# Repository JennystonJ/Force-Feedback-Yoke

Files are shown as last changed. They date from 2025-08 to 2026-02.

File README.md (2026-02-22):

# Force Feedback Yoke
A DIY force feedback flight simulator yoke using brushless motors, load cells, and custom firmware to provide simulated control forces.

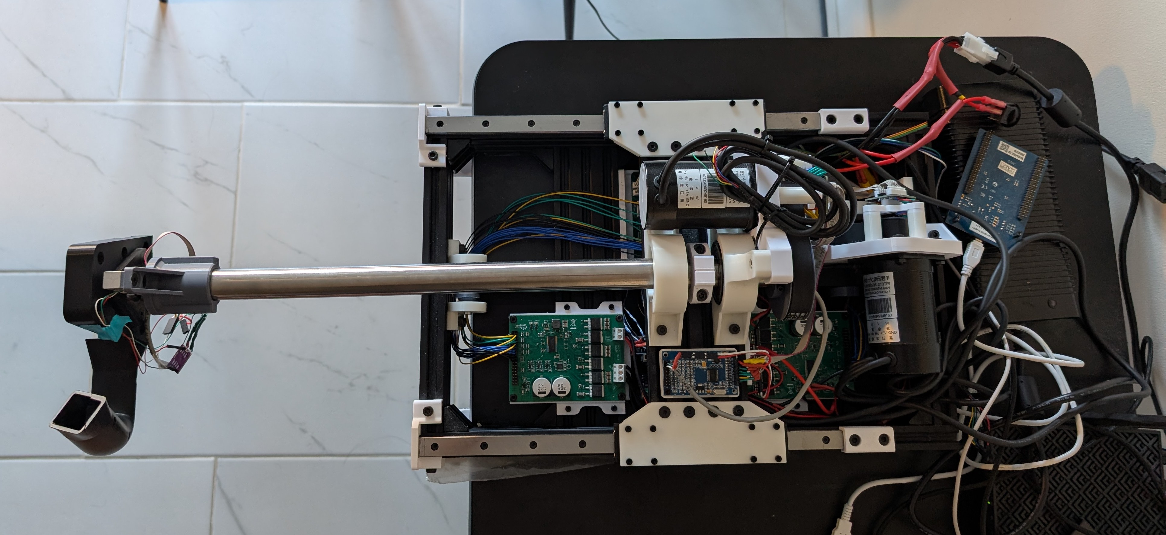
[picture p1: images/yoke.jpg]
Yoke Picture


---

## Overview
- BLDC motors for pitch and roll using torque control.
- Support for load cells. Currently used for force feedback assist (reduces drag felt by user).
- STM32 microcontroller running custom firmware with FOC inspired by SimpleFOC.
- Desktop app for monitoring, setting parameters, handling communication between device and Microsoft Flight Simulator, and calculating forces.

## Features
- Support for 2 axis current/torque control.
- Force feedback assist using load cells to reduce drag.
- USB HID communication.
- Support for constant, spring, and damper effects on both axes.
- Axes travel is software adjustable using the motor as a virtual stopper.

## Technical Details
- Motors: 2 * 57BL95S06-210TF9
- Motor Drivers: 2 * DRV8301 boards
- Microcontroller: STM32H743VGT6
- Sensors:
	- 2 * three phase shunt-based in-line current sensors (INA241)
	- 2 * encoders using AB output (65536 CPR) for lower latency (MT6835)
	- 2 * load cells (20kg) (roll load cell support for mechanical is in progress)
- Software: C firmware, C# desktop app

## Mechanical
- Total pitch travel: ~177 mm, roll travel: ~270 deg
- 3D printed components, aluminum V-slot extrusion for frame. T-slot is also compatible.
- Bearings on all axes, two linear guide rails for linear motion on pitch axis.
- Two-stage belt drive for pitch axis, single belt for roll axis.
- Designed to be modular.

## Desktop App
- Displays live axes positions, and axes force/torque
- Implements custom USB HID communication with device and communication with Microsoft Flight Simulator through SimConnect API.
- Currently supports 2 different force feedback effects, with more being added and existing effects being refined:
	- Supported effects
		- Airspeed stiffness (increases centering force with airspeed)
		- Elevator weight (a constant elevator down force with engine RPM dependent self-centering force).
- Adjustable gains for all force feedback effects in GUI for both pitch and roll axes.
- Travel for both axes are adjustable in GUI.

## Acknowledgements
Algorithms (Clarke & Park transforms) from [SimpleFOC](https://github.com/simplefoc/Arduino-FOC) (MIT License). See LICENSES/LICENSE-SIMPLEFOC.txt for full license.

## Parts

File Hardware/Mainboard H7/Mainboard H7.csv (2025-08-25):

Reference | Qty | Value | DNP | Exclude from BOM | Exclude from Board | Footprint | Datasheet
C1,C2,C3,C4,C5,C6,C7,C8 | 8 | 0.1uF |  |  |  | Capacitor_SMD:C_0603_1608Metric_Pad1.08x0.95mm_HandSolder | ~
J1 | 1 | Encoder_2 |  |  |  | Connector_JST:JST_PH_B9B-PH-K_1x09_P2.00mm_Vertical | ~
J2 | 1 | Encoder_1_AB |  |  |  | Connector_JST:JST_PH_B4B-PH-K_1x04_P2.00mm_Vertical | ~
J3 | 1 | M1_Communication |  |  |  | Connector_PinHeader_2.54mm:PinHeader_2x04_P2.54mm_Vertical | ~
J4 | 1 | M1_Driver |  |  |  | Connector_PinHeader_2.54mm:PinHeader_2x06_P2.54mm_Vertical | ~
J5 | 1 | M2_Communication |  |  |  | Connector_PinHeader_2.54mm:PinHeader_2x04_P2.54mm_Vertical | ~
J6 | 1 | M2_Driver |  |  |  | Connector_PinHeader_2.54mm:PinHeader_2x06_P2.54mm_Vertical | ~
J7 | 1 | I2C Expansion 1 |  |  |  | Connector_JST:JST_PH_B6B-PH-K_1x06_P2.00mm_Vertical | ~
J8 | 1 | I2C Expansion 2 |  |  |  | Connector_JST:JST_PH_B6B-PH-K_1x06_P2.00mm_Vertical | ~
J9 | 1 | Encoder_1 |  |  |  | Connector_JST:JST_PH_B9B-PH-K_1x09_P2.00mm_Vertical | ~
J10 | 1 | Encoder_2_AB |  |  |  | Connector_JST:JST_PH_B4B-PH-K_1x04_P2.00mm_Vertical | ~
J11 | 1 | ADC_2 |  |  |  | Connector_JST:JST_PH_B10B-PH-K_1x10_P2.00mm_Vertical | ~
J12 | 1 | ADC_1 |  |  |  | Connector_JST:JST_PH_B10B-PH-K_1x10_P2.00mm_Vertical | ~
J13 | 1 | Yoke_Handle |  |  |  | Connector_JST:JST_PH_B10B-PH-K_1x10_P2.00mm_Vertical | ~
J14 | 1 | M1_Current_Sense |  |  |  | Connector_JST:JST_PH_B8B-PH-K_1x08_P2.00mm_Vertical | ~
J15 | 1 | M2_Current_Sense |  |  |  | Connector_JST:JST_PH_B8B-PH-K_1x08_P2.00mm_Vertical | ~
J16 | 1 | PROBE |  |  |  | Connector_PinHeader_2.54mm:PinHeader_1x03_P2.54mm_Vertical | ~
J17 | 1 | UART |  |  |  | Connector_PinHeader_2.54mm:PinHeader_1x04_P2.54mm_Vertical | ~
J18 | 1 | Power Output |  |  |  | Connector_PinHeader_2.54mm:PinHeader_1x02_P2.54mm_Vertical | ~
J19 | 1 | CAN |  |  |  | Connector_PinHeader_2.54mm:PinHeader_1x05_P2.54mm_Vertical | ~
R1,R2,R3,R4 | 4 | 10k |  |  |  | Resistor_SMD:R_0603_1608Metric_Pad0.98x0.95mm_HandSolder | ~
R5,R6,R7,R8 | 4 | 4.7k |  |  |  | Resistor_SMD:R_0603_1608Metric_Pad0.98x0.95mm_HandSolder | ~
R9 | 1 | 1k |  |  |  | Resistor_SMD:R_0603_1608Metric_Pad0.98x0.95mm_HandSolder | ~
SW1 | 1 | SW_Push |  |  |  | Connector_JST:JST_PH_B2B-PH-K_1x02_P2.00mm_Vertical | ~
U1 | 1 | ~ |  |  |  | FK743M3:FK743M3-VGT6

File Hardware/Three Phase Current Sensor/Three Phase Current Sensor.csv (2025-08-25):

Reference | Qty | Value | DNP | Exclude from BOM | Exclude from Board | Footprint | Datasheet
C1,C8 | 2 | 10uF |  |  |  | Capacitor_SMD:C_0603_1608Metric | ~
C2 | 1 | 10nF |  |  |  | Capacitor_SMD:C_0603_1608Metric | ~
C3,C4,C5,C6,C7 | 5 | 0.1uF |  |  |  | Capacitor_SMD:C_0603_1608Metric | ~
H1,H2 | 2 | MountingHole |  | Excluded from BOM |  | MountingHole:MountingHole_2.2mm_M2 | ~
J1 | 1 | Current Sense Out |  |  |  | Connector_JST:JST_PH_B8B-PH-K_1x08_P2.00mm_Vertical | ~
J2,J3,J4 | 3 | Conn_01x02 |  |  |  | TB005_762_02BE:CUI_TB005-762-02BE | ~
J5 | 1 | Power |  |  |  | Connector_Molex:Molex_KK-254_AE-6410-02A_1x02_P2.54mm_Vertical | ~
R1,R2 | 2 | 10k |  |  |  | Resistor_SMD:R_0603_1608Metric | ~
R3,R4,R5 | 3 | 5m |  |  |  | Resistor_SMD:R_2512_6332Metric | ~
U1 | 1 | TLV9151IDBVR |  |  |  | TLV9151:DBV0005A-MFG | TLV9151IDBVR
U2,U3,U4 | 3 | INA240A1D |  |  |  | Package_SO:SOIC-8_3.9x4.9mm_P1.27mm | http://www.ti.com/lit/ds/symlink/ina240.pdf

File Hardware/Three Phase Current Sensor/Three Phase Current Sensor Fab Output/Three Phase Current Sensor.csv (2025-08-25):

Reference | Qty | Value | DNP | Exclude from BOM | Exclude from Board | Footprint | Datasheet
C1,C8 | 2 | 10uF |  |  |  | Capacitor_SMD:C_0603_1608Metric | ~
C2 | 1 | 10nF |  |  |  | Capacitor_SMD:C_0603_1608Metric | ~
C3,C4,C5,C6,C7 | 5 | 0.1uF |  |  |  | Capacitor_SMD:C_0603_1608Metric | ~
H1,H2,H3,H4 | 4 | MountingHole |  | Excluded from BOM |  | MountingHole:MountingHole_2.2mm_M2 | ~
J1 | 1 | Current Sense Out |  |  |  | Connector_JST:JST_PH_B8B-PH-K_1x08_P2.00mm_Vertical | ~
J2,J3,J4 | 3 | Conn_01x02 |  |  |  | TerminalBlock_Phoenix:TerminalBlock_Phoenix_MKDS-1,5-2-5.08_1x02_P5.08mm_Horizontal | ~
J5 | 1 | Power |  |  |  | Connector_Molex:Molex_KK-254_AE-6410-02A_1x02_P2.54mm_Vertical | ~
R1,R2 | 2 | 10k |  |  |  | Resistor_SMD:R_0603_1608Metric | ~
R3,R4,R5 | 3 | 5m |  |  |  | Resistor_SMD:R_2512_6332Metric | ~
R6 | 1 | 50 |  |  |  | Resistor_SMD:R_0603_1608Metric | ~
U1 | 1 | LMV796MFX |  |  |  | TLV9151:DBV0005A-MFG | TLV9151IDBVR
U2,U3,U4 | 3 | INA241A2IDR |  |  |  | Package_SO:SOIC-8_3.9x4.9mm_P1.27mm | http://www.ti.com/lit/ds/symlink/ina240.pdf

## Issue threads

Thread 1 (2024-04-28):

yoke

1766029053, 2024-04-28:
This project looks cool, are you still working on it

JennystonJ, 2024-05-01:
The force feedback yoke is still in development. While there was a hiatus, I've been focusing on designing its mechanical parts, mostly using 3D printed parts and aluminum extrusion. I plan on returning to the code soon. Thank you for your interest. Feel free to ask if you have any more questions!

1766029053, 2024-05-13:
Do you have any relevant communication platform, so as to facilitate our communication

JennystonJ, 2024-07-01:
I've created a Discord server for the project. Here is the link: https://discord.gg/AJm64B3pnq

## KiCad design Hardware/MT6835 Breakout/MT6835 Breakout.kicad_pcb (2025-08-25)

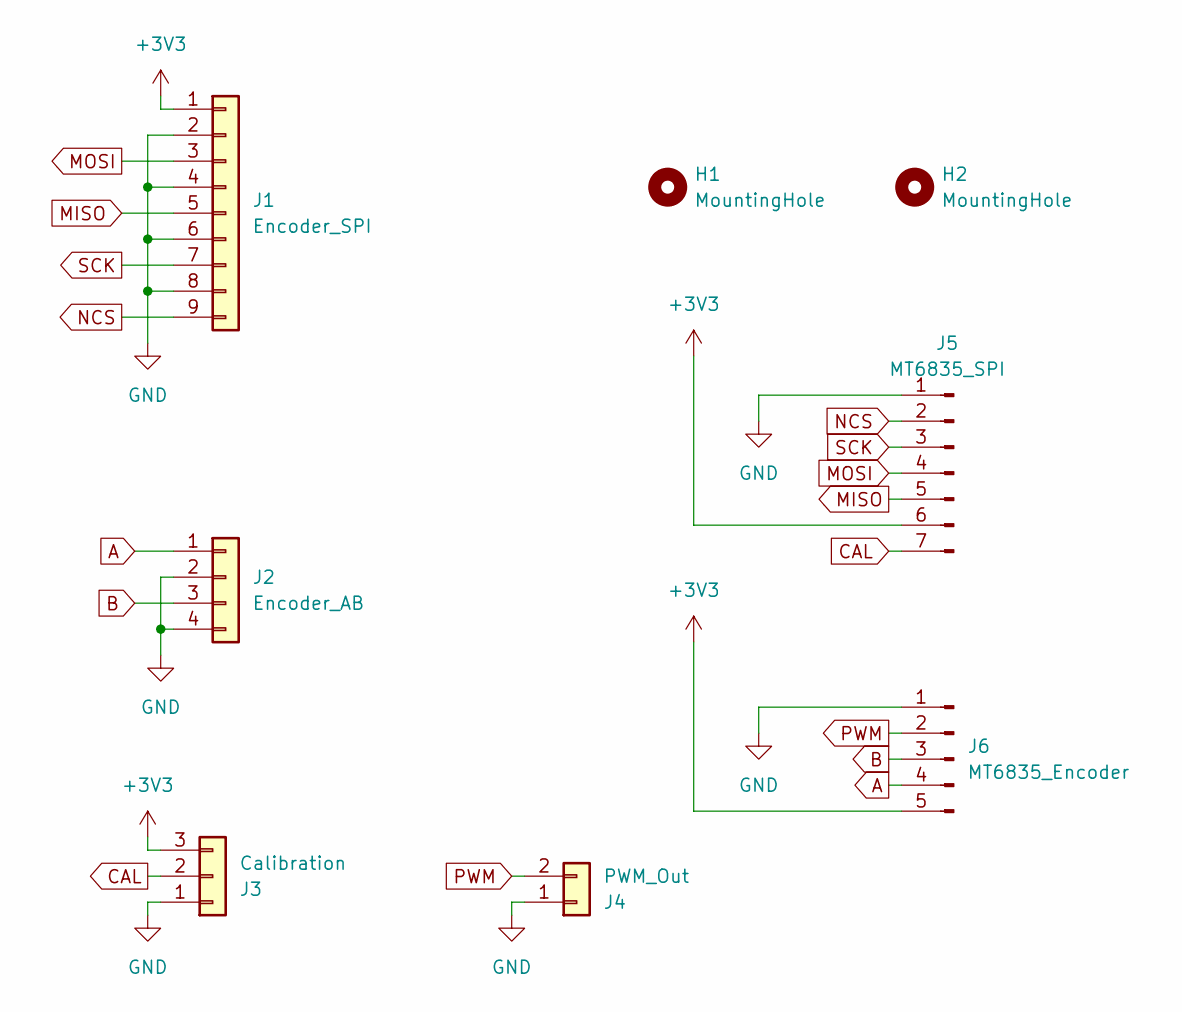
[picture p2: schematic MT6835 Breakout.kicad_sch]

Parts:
H1, H2: MountingHole; MountingHole_2.2mm_M2
J1: Encoder_SPI; JST_PH_B9B-PH-K_1x09_P2.00mm_Vertical
J2: Encoder_AB; JST_PH_B4B-PH-K_1x04_P2.00mm_Vertical
J3: Calibration; PinHeader_1x03_P2.54mm_Vertical
J4: PWM_Out; PinHeader_1x02_P2.54mm_Vertical
J5: MT6835_SPI; PinHeader_1x07_P2.54mm_Vertical
J6: MT6835_Encoder; PinHeader_1x05_P2.54mm_Vertical

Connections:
+3V3: J1.1, J3.3, J5.6, J6.5
A: J2.1, J6.4
B: J2.3, J6.3
CAL: J3.2, J5.7
GND: J1.2, J1.4, J1.6, J1.8, J2.2, J2.4, J3.1, J4.1, J5.1, J6.1
MISO: J1.5, J5.5
MOSI: J1.3, J5.4
NCS: J1.9, J5.2
PWM: J4.2, J6.2
SCK: J1.7, J5.3

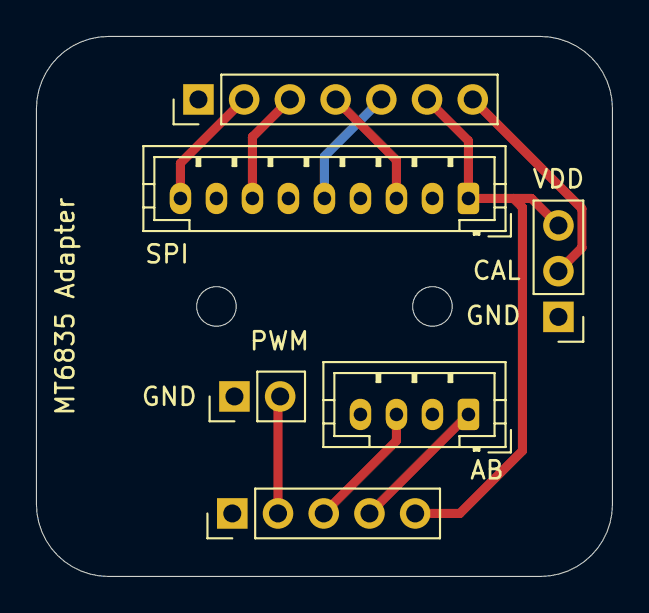
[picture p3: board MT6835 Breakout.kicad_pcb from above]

Board: 2 copper layers, 32.0 x 30.0 mm, 8 parts (0 on the bottom side), 10 nets.

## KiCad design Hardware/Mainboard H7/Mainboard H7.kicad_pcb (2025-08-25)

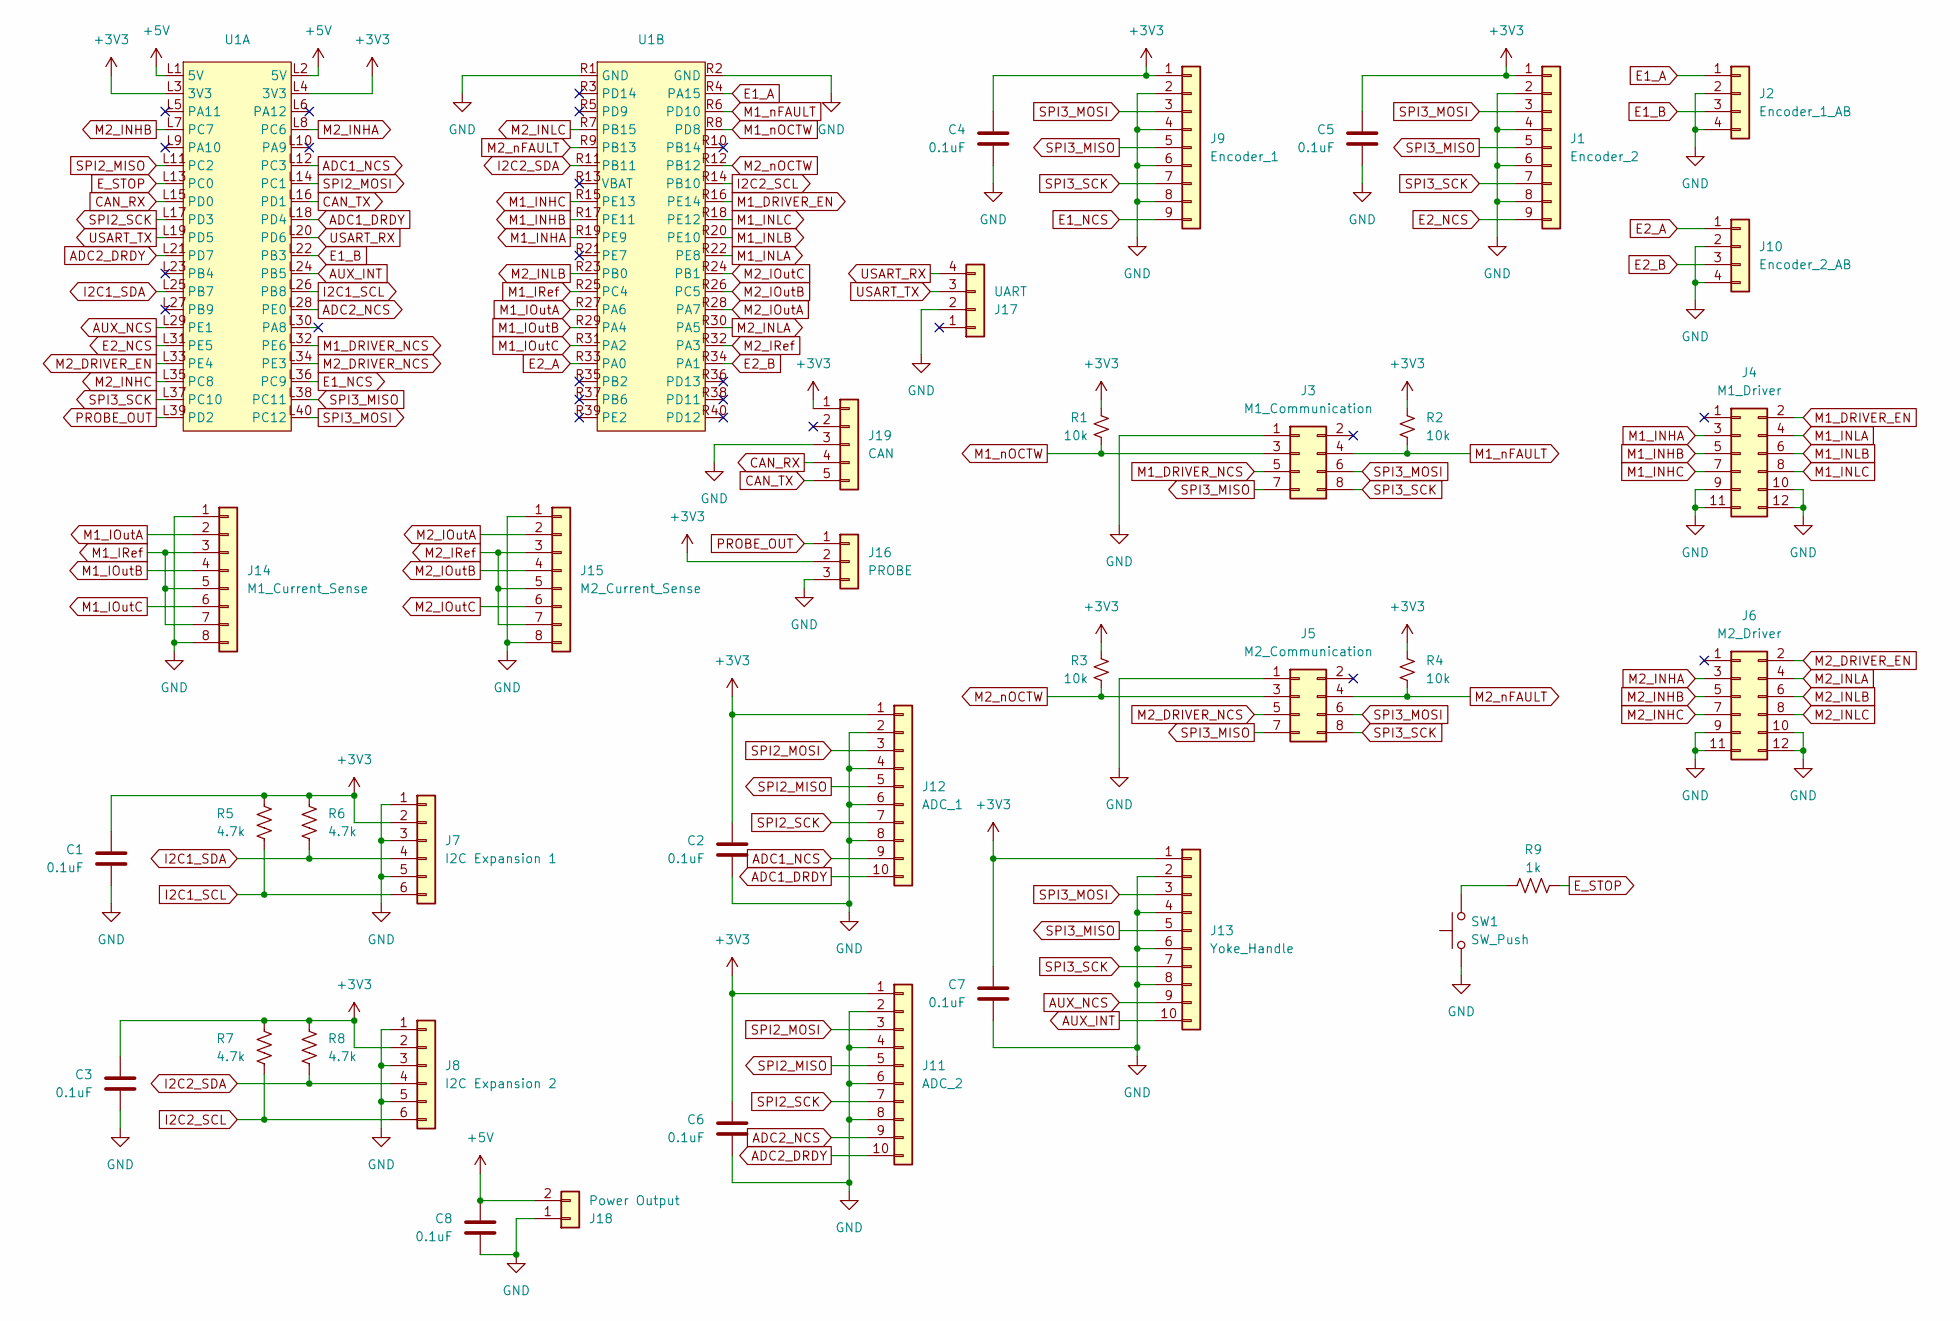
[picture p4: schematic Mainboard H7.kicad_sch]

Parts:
C1, C2, C3, C4, C5, C6, C7, C8: 0.1uF; C_0603_1608Metric_Pad1.08x0.95mm_HandSolder
J1: Encoder_2; JST_PH_B9B-PH-K_1x09_P2.00mm_Vertical
J2: Encoder_1_AB; JST_PH_B4B-PH-K_1x04_P2.00mm_Vertical
J3: M1_Communication; PinHeader_2x04_P2.54mm_Vertical
J4: M1_Driver; PinHeader_2x06_P2.54mm_Vertical
J5: M2_Communication; PinHeader_2x04_P2.54mm_Vertical
J6: M2_Driver; PinHeader_2x06_P2.54mm_Vertical
J7: I2C Expansion 1; JST_PH_B6B-PH-K_1x06_P2.00mm_Vertical
J8: I2C Expansion 2; JST_PH_B6B-PH-K_1x06_P2.00mm_Vertical
J9: Encoder_1; JST_PH_B9B-PH-K_1x09_P2.00mm_Vertical
J10: Encoder_2_AB; JST_PH_B4B-PH-K_1x04_P2.00mm_Vertical
J11: ADC_2; JST_PH_B10B-PH-K_1x10_P2.00mm_Vertical
J12: ADC_1; JST_PH_B10B-PH-K_1x10_P2.00mm_Vertical
J13: Yoke_Handle; JST_PH_B10B-PH-K_1x10_P2.00mm_Vertical
J14: M1_Current_Sense; JST_PH_B8B-PH-K_1x08_P2.00mm_Vertical
J15: M2_Current_Sense; JST_PH_B8B-PH-K_1x08_P2.00mm_Vertical
J16: PROBE; PinHeader_1x03_P2.54mm_Vertical
J17: UART; PinHeader_1x04_P2.54mm_Vertical
J18: Power Output; PinHeader_1x02_P2.54mm_Vertical
J19: CAN; PinHeader_1x05_P2.54mm_Vertical
R1, R2, R3, R4: 10k; R_0603_1608Metric_Pad0.98x0.95mm_HandSolder
R5, R6, R7, R8: 4.7k; R_0603_1608Metric_Pad0.98x0.95mm_HandSolder
R9: 1k; R_0603_1608Metric_Pad0.98x0.95mm_HandSolder
SW1: SW_Push; JST_PH_B2B-PH-K_1x02_P2.00mm_Vertical
U1: FK743M3-VGT6

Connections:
+3V3: C1.1, C2.1, C3.1, C4.1, C5.1, C6.1, C7.1, J1.1, J7.2, J8.2, J9.1, J11.1, J12.1, J13.1, J16.2, J19.1, R1.1, R2.1, R3.1, R4.1, R5.1, R6.1, R7.1, R8.1, U1.L3 (3V3), U1.L4 (3V3)
+5V: C8.1, J18.2, U1.L1 (5V), U1.L2 (5V)
ADC1_DRDY: J12.10, U1.L18 (PD4)
ADC1_NCS: J12.9, U1.L12 (PC3)
ADC2_DRDY: J11.10, U1.L21 (PD7)
ADC2_NCS: J11.9, U1.L28 (PE0)
AUX_INT: J13.10, U1.L24 (PB5)
AUX_NCS: J13.9, U1.L29 (PE1)
CAN_RX: J19.4, U1.L15 (PD0)
CAN_TX: J19.5, U1.L16 (PD1)
E1_A: J2.1, U1.R4 (PA15)
E1_B: J2.3, U1.L22 (PB3)
E1_NCS: J9.9, U1.L36 (PC9)
E2_A: J10.1, U1.R33 (PA0)
E2_B: J10.3, U1.R34 (PA1)
E2_NCS: J1.9, U1.L31 (PE5)
E_STOP: R9.1, U1.L13 (PC0)
GND: C1.2, C2.2, C3.2, C4.2, C5.2, C6.2, C7.2, C8.2, J1.2, J1.4, J1.6, J1.8, J2.2, J2.4, J3.1, J4.9, J4.10, J4.11, J4.12, J5.1, J6.9, J6.10, J6.11, J6.12, J7.1, J7.3, J7.5, J8.1, J8.3, J8.5, J9.2, J9.4, J9.6, J9.8, J10.2, J10.4, J11.2, J11.4, J11.6, J11.8, J12.2, J12.4, J12.6, J12.8, J13.2, J13.4, J13.6, J13.8, J14.1, J14.8, J15.1, J15.8, J16.3, J17.2, J18.1, J19.3, SW1.1, U1.R1 (GND), U1.R2 (GND)
I2C1_SCL: J7.6, R5.2, U1.L26 (PB8)
I2C1_SDA: J7.4, R6.2, U1.L25 (PB7)
I2C2_SCL: J8.6, R7.2, U1.R14 (PB10)
I2C2_SDA: J8.4, R8.2, U1.R11 (PB11)
M1_DRIVER_EN: J4.2, U1.R16 (PE14)
M1_DRIVER_NCS: J3.5, U1.L32 (PE6)
M1_INHA: J4.3, U1.R19 (PE9)
M1_INHB: J4.5, U1.R17 (PE11)
M1_INHC: J4.7, U1.R15 (PE13)
M1_INLA: J4.4, U1.R22 (PE8)
M1_INLB: J4.6, U1.R20 (PE10)
M1_INLC: J4.8, U1.R18 (PE12)
M1_IOutA: J14.2, U1.R27 (PA6)
M1_IOutB: J14.4, U1.R29 (PA4)
M1_IOutC: J14.6, U1.R31 (PA2)
M1_IRef: J14.3, J14.5, J14.7, U1.R25 (PC4)
M1_nFAULT: J3.4, R2.2, U1.R6 (PD10)
M1_nOCTW: J3.3, R1.2, U1.R8 (PD8)
M2_DRIVER_EN: J6.2, U1.L33 (PE4)
M2_DRIVER_NCS: J5.5, U1.L34 (PE3)
M2_INHA: J6.3, U1.L8 (PC6)
M2_INHB: J6.5, U1.L7 (PC7)
M2_INHC: J6.7, U1.L35 (PC8)
M2_INLA: J6.4, U1.R30 (PA5)
M2_INLB: J6.6, U1.R23 (PB0)
M2_INLC: J6.8, U1.R7 (PB15)
M2_IOutA: J15.2, U1.R28 (PA7)
M2_IOutB: J15.4, U1.R26 (PC5)
M2_IOutC: J15.6, U1.R24 (PB1)
M2_IRef: J15.3, J15.5, J15.7, U1.R32 (PA3)
M2_nFAULT: J5.4, R4.2, U1.R9 (PB13)
M2_nOCTW: J5.3, R3.2, U1.R12 (PB12)
unnamed: R9.2, SW1.2
PROBE_OUT: J16.1, U1.L39 (PD2)
SPI2_MISO: J11.5, J12.5, U1.L11 (PC2)
SPI2_MOSI: J11.3, J12.3, U1.L14 (PC1)
SPI2_SCK: J11.7, J12.7, U1.L17 (PD3)
SPI3_MISO: J1.5, J3.7, J5.7, J9.5, J13.5, U1.L38 (PC11)
SPI3_MOSI: J1.3, J3.6, J5.6, J9.3, J13.3, U1.L40 (PC12)
SPI3_SCK: J1.7, J3.8, J5.8, J9.7, J13.7, U1.L37 (PC10)
USART_RX: J17.4, U1.L20 (PD6)
USART_TX: J17.3, U1.L19 (PD5)

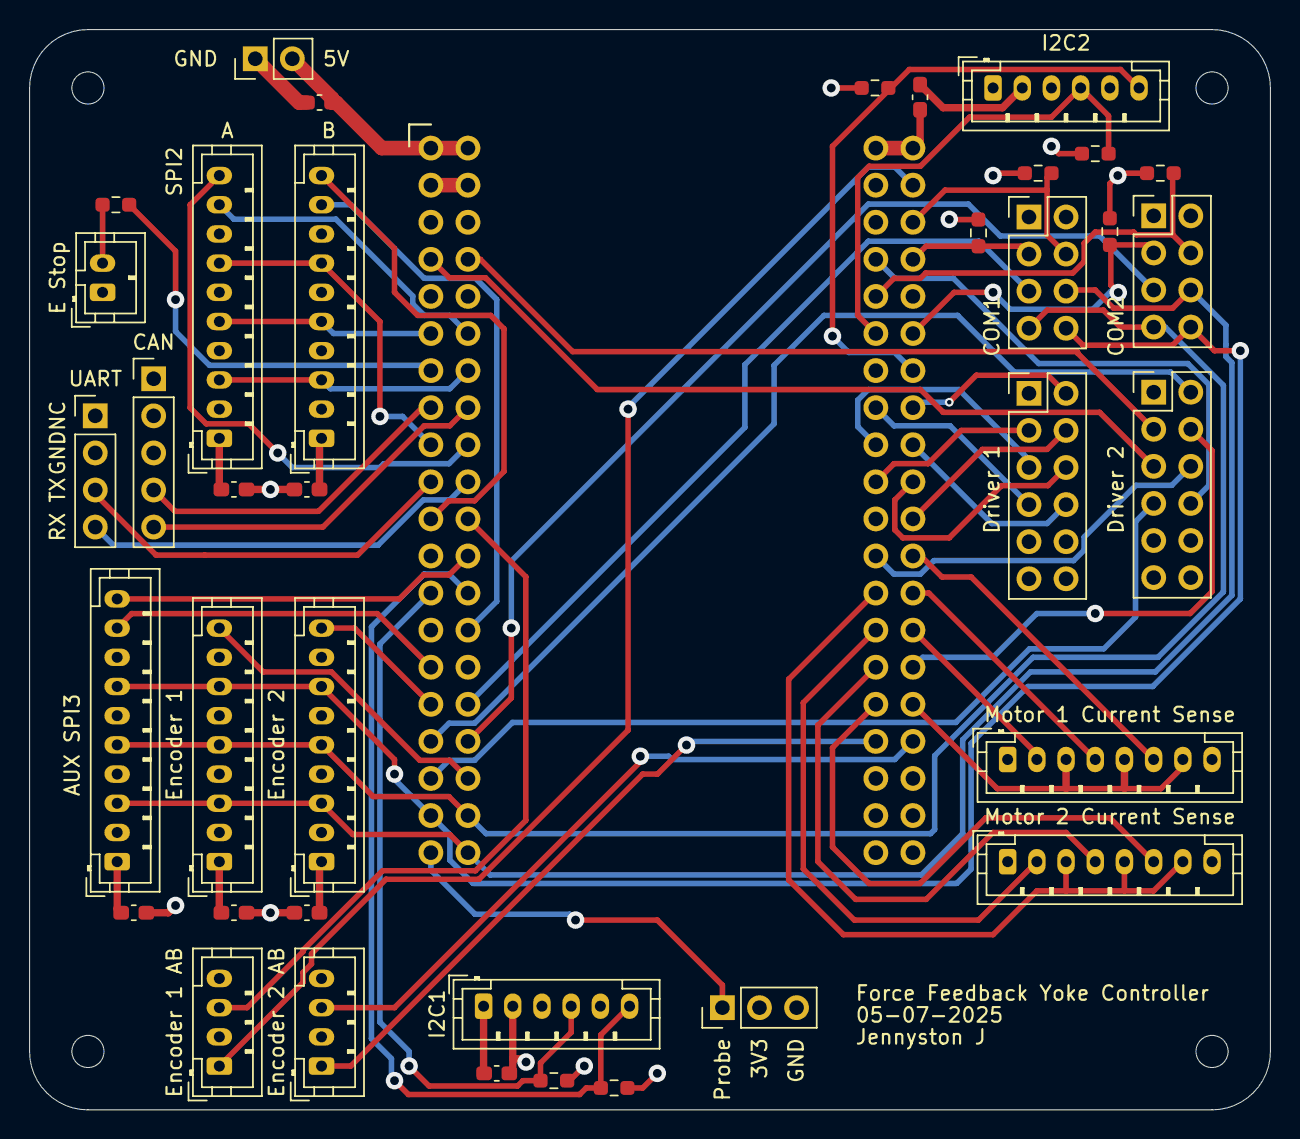
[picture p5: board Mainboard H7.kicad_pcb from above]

Board: 4 copper layers, 85.0 x 74.0 mm, 38 parts (0 on the bottom side), 60 nets.

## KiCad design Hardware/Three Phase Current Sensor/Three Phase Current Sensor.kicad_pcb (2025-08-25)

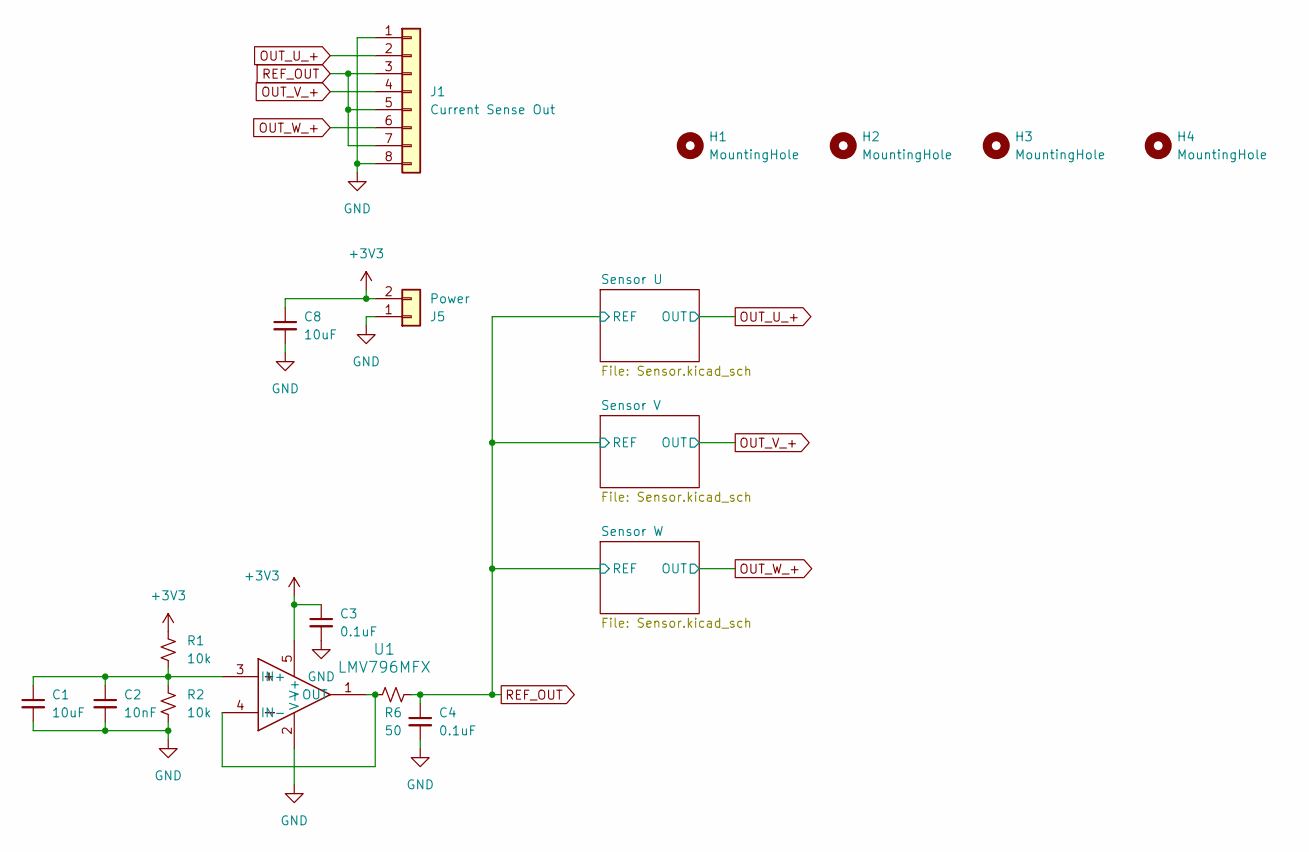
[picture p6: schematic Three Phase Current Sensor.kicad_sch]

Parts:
C1, C8: 10uF; C_0603_1608Metric
C2: 10nF; C_0603_1608Metric
C3, C4: 0.1uF; C_0603_1608Metric
H1, H2, H3, H4: MountingHole; MountingHole_2.2mm_M2
J1: Current Sense Out; JST_PH_B8B-PH-K_1x08_P2.00mm_Vertical
J5: Power; Molex_KK-254_AE-6410-02A_1x02_P2.54mm_Vertical
R1, R2: 10k; R_0603_1608Metric
R6: 50; R_0603_1608Metric
U1: LMV796MFX; DBV0005A-MFG

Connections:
+3V3: C3.1, C8.1, J5.2, R1.2, U1.5 (V+); also elsewhere on the board
GND: C1.2, C2.2, C3.2, C4.2, C8.2, J1.1, J1.8, J5.1, R2.1, U1.2 (V-); also elsewhere on the board
unnamed: C1.1, C2.1, R1.1, R2.2, U1.3 (IN+)
unnamed: R6.2, U1.1 (OUT), U1.4 (IN-)
OUT_U_+: J1.2; also elsewhere on the board
OUT_V_+: J1.4; also elsewhere on the board
OUT_W_+: J1.6; also elsewhere on the board
REF_OUT: C4.1, J1.3, J1.5, J1.7, R6.1; also elsewhere on the board

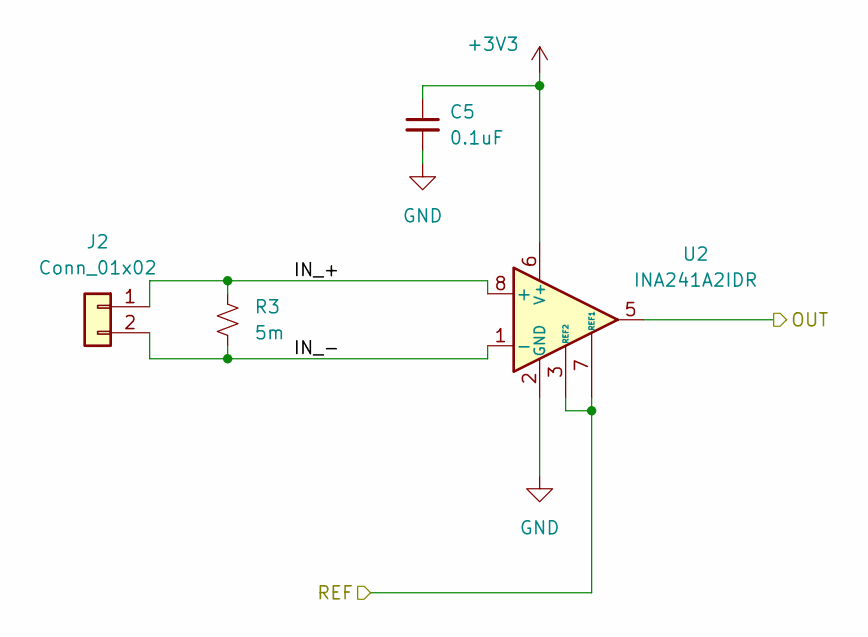
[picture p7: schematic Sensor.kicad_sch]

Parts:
C5: 0.1uF; C_0603_1608Metric
J2: Conn_01x02; TerminalBlock_Phoenix_MKDS-1,5-2-5.08_1x02_P5.08mm_Horizont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
R3: 5m; R_2512_6332Metric
U2: INA241A2IDR; SOIC-8_3.9x4.9mm_P1.27mm

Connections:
+3V3: C5.1, U2.6 (V+); also elsewhere on the board
/Sensor U/IN_+: J2.1, R3.1, U2.8 (+)
/Sensor U/IN_-: J2.2, R3.2, U2.1 (-)
GND: C5.2, U2.2 (GND), U2.4 (GND); also elsewhere on the board
OUT_U_+: U2.5; also elsewhere on the board
REF_OUT: U2.3 (REF2), U2.7 (REF1); also elsewhere on the board

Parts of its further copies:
C6, C7: 0.1uF; C_0603_1608Metric
J3, J4: Conn_01x02; TerminalBlock_Phoenix_MKDS-1,5-2-5.08_1x02_P5.08mm_Horizont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
R4, R5: 5m; R_2512_6332Metric
U3, U4: INA241A2IDR; SOIC-8_3.9x4.9mm_P1.27mm

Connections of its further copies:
+3V3: C6.1, C7.1, U3.6 (V+), U4.6 (V+); also elsewhere on the board
/Sensor V/IN_+: J3.1, R4.1, U3.8 (+)
/Sensor V/IN_-: J3.2, R4.2, U3.1 (-)
/Sensor W/IN_+: J4.1, R5.1, U4.8 (+)
/Sensor W/IN_-: J4.2, R5.2, U4.1 (-)
GND: C6.2, C7.2, U3.2 (GND), U3.4 (GND), U4.2 (GND), U4.4 (GND); also elsewhere on the board
OUT_V_+: U3.5; also elsewhere on the board
OUT_W_+: U4.5; also elsewhere on the board
REF_OUT: U3.3 (REF2), U3.7 (REF1), U4.3 (REF2), U4.7 (REF1); also elsewhere on the board

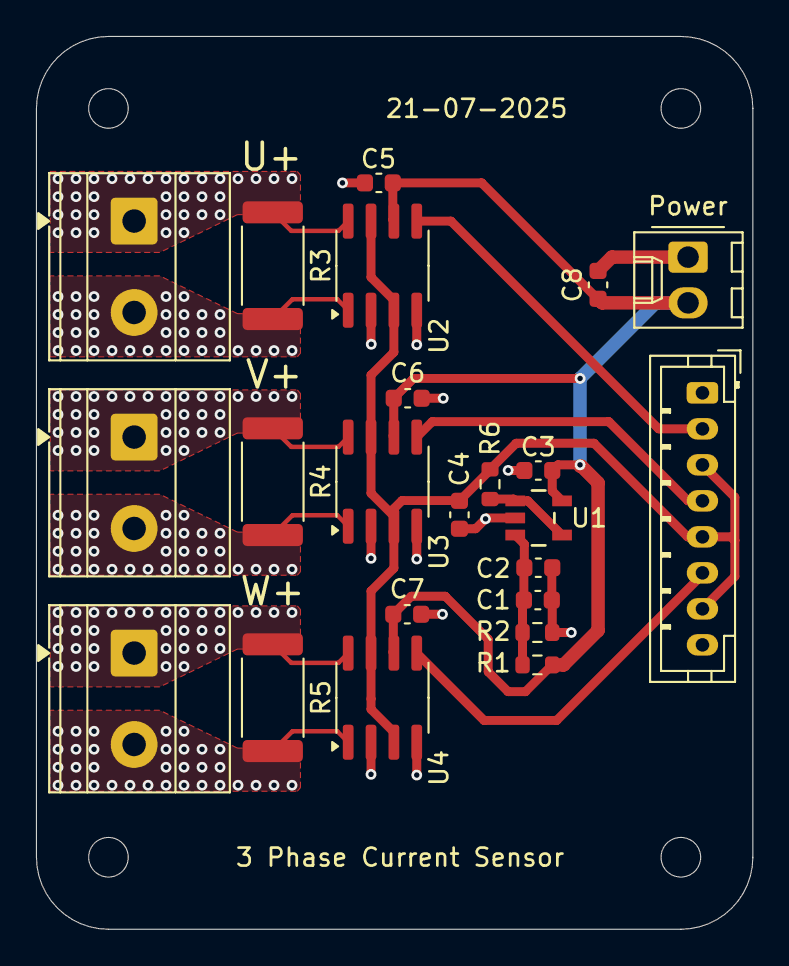
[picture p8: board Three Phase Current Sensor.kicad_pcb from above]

Board: 2 copper layers, 39.8 x 49.6 mm, 27 parts (0 on the bottom side), 14 nets.

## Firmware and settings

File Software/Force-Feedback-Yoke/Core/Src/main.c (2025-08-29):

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
/* Includes ------------------------------------------------------------------*/
#include "main.h"
#include "usb_device.h"

/* USER CODE BEGIN Includes */
#include "bsp.h"
#include "bsp_it.h"
#include "app.h"
/* USER CODE END Includes */

ADC_HandleTypeDef hadc1;
ADC_HandleTypeDef hadc2;

FDCAN_HandleTypeDef hfdcan1;

I2C_HandleTypeDef hi2c1;
I2C_HandleTypeDef hi2c2;

QSPI_HandleTypeDef hqspi;

SPI_HandleTypeDef hspi2;
SPI_HandleTypeDef hspi3;
DMA_HandleTypeDef hdma_spi2_rx;
DMA_HandleTypeDef hdma_spi2_tx;

TIM_HandleTypeDef htim1;
TIM_HandleTypeDef htim2;
TIM_HandleTypeDef htim3;
TIM_HandleTypeDef htim5;
TIM_HandleTypeDef htim6;
TIM_HandleTypeDef htim7;
TIM_HandleTypeDef htim8;
TIM_HandleTypeDef htim12;

UART_HandleTypeDef huart1;
UART_HandleTypeDef huart2;
DMA_HandleTypeDef hdma_usart2_rx;
DMA_HandleTypeDef hdma_usart2_tx;

void SystemClock_Config(void);
void PeriphCommonClock_Config(void);
static void MPU_Config(void);
static void MX_GPIO_Init(void);
static void MX_DMA_Init(void);
static void MX_TIM1_Init(void);
static void MX_ADC1_Init(void);
static void MX_ADC2_Init(void);
static void MX_TIM8_Init(void);
static void MX_I2C1_Init(void);
static void MX_I2C2_Init(void);
static void MX_USART2_UART_Init(void);
static void MX_SPI2_Init(void);
static void MX_FDCAN1_Init(void);
static void MX_TIM2_Init(void);
static void MX_TIM5_Init(void);
static void MX_QUADSPI_Init(void);
static void MX_SPI3_Init(void);
static void MX_USART1_UART_Init(void);
static void MX_TIM6_Init(void);
static void MX_TIM7_Init(void);
static void MX_TIM12_Init(void);
static void MX_TIM3_Init(void);
/* USER CODE BEGIN 0 */
void HAL_GPIO_EXTI_Callback(uint16_t GPIO_Pin) {
	BspIT_EXTIIT(GPIO_Pin);
}

void HAL_TIM_PeriodElapsedCallback(TIM_HandleTypeDef *htim) {
	BspIT_TimIT(htim);
}

void HAL_TIM_OC_DelayElapsedCallback(TIM_HandleTypeDef *htim) {
//	GPIOSetState(&probeGpio, !GPIOGetState(&probeGpio));
}

void HAL_ADCEx_InjectedConvCpltCallback(ADC_HandleTypeDef *hadc) {
	BspIT_ADCIT(hadc);
}

void HAL_ADC_LevelOutOfWindowCallback(ADC_HandleTypeDef* hadc) {
	BspIT_ADCWatchDogIT(hadc);
}

void HAL_SPI_TxRxCpltCallback(SPI_HandleTypeDef *hspi) {
	BspIT_SPIIT(hspi);
}

void HAL_UART_TxCpltCallback(UART_HandleTypeDef *huart) {
	BspIT_UARTTxCpltIT(huart);
}

void HAL_UART_RxCpltCallback(UART_HandleTypeDef *huart) {
	BspIT_UARTRxCpltIT(huart);
}

/* USER CODE END 0 */

/**
  * @brief  The application entry point.
  * @retval int
  */
int main(void)
{

  /* MPU Configuration--------------------------------------------------------*/
  MPU_Config();

  /* Enable the CPU Cache */

  /* Enable I-Cache---------------------------------------------------------*/
  SCB_EnableICache();

  /* MCU Configuration--------------------------------------------------------*/

  /* Reset of all peripherals, Initializes the Flash interface and the Systick. */
  HAL_Init();

  /* Configure the system clock */
  SystemClock_Config();

  /* Configure the peripherals common clocks */
  PeriphCommonClock_Config();

  /* Initialize all configured peripherals */
  MX_GPIO_Init();
  MX_DMA_Init();
  MX_TIM1_Init();
  MX_ADC1_Init();
  MX_ADC2_Init();
  MX_TIM8_Init();
  MX_I2C1_Init();
  MX_I2C2_Init();
  MX_USART2_UART_Init();
  MX_SPI2_Init();
  MX_FDCAN1_Init();
  MX_TIM2_Init();
  MX_TIM5_Init();
  MX_QUADSPI_Init();
  MX_SPI3_Init();
  MX_USART1_UART_Init();
  MX_TIM6_Init();
  MX_TIM7_Init();
  MX_TIM12_Init();
  MX_TIM3_Init();
  MX_USB_DEVICE_Init();
  /* USER CODE BEGIN 2 */
  Bsp_Init();
  Application_Init();
  Application_Run();
  /* USER CODE END 2 */

  /* Infinite loop */
  /* USER CODE BEGIN WHILE */
  while (1)
  {
    /* USER CODE END WHILE */

    /* USER CODE BEGIN 3 */
  }
  /* USER CODE END 3 */
}

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
 /* MPU Configuration */

void MPU_Config(void)
{
  MPU_Region_InitTypeDef MPU_InitStruct = {0};

  /* Disables the MPU */
  HAL_MPU_Disable();

  /** Initializes and configures the Region and the memory to be protected
  */
  MPU_InitStruct.Enable = MPU_REGION_ENABLE;
  MPU_InitStruct.Number = MPU_REGION_NUMBER0;
  MPU_InitStruct.BaseAddress = 0x0;
  MPU_InitStruct.Size = MPU_REGION_SIZE_4GB;
  MPU_InitStruct.SubRegionDisable = 0x87;
  MPU_InitStruct.TypeExtField = MPU_TEX_LEVEL0;
  MPU_InitStruct.AccessPermission = MPU_REGION_NO_ACCESS;
  MPU_InitStruct.DisableExec = MPU_INSTRUCTION_ACCESS_DISABLE;
  MPU_InitStruct.IsShareable = MPU_ACCESS_SHAREABLE;
  MPU_InitStruct.IsCacheable = MPU_ACCESS_NOT_CACHEABLE;
  MPU_InitStruct.IsBufferable = MPU_ACCESS_NOT_BUFFERABLE;

  HAL_MPU_ConfigRegion(&MPU_InitStruct);
  /* Enables the MPU */
  HAL_MPU_Enable(MPU_PRIVILEGED_DEFAULT);

}

/**
  * @brief  This function is executed in case of error occurrence.
  * @retval None
  */
void Error_Handler(void)
{
  /* USER CODE BEGIN Error_Handler_Debug */
  /* User can add his own implementation to report the HAL error return state */
  __disable_irq();
  while (1)
  {
  }
  /* USER CODE END Error_Handler_Debug */
}

#ifdef  USE_FULL_ASSERT
/**
  * @brief  Reports the name of the source file and the source line number
  *         where the assert_param error has occurred.
  * @param  file: pointer to the source file name
  * @param  line: assert_param error line source number
  * @retval None
  */
void assert_failed(uint8_t *file, uint32_t line)
{
  /* USER CODE BEGIN 6 */
  /* User can add his own implementation to report the file name and line number,
     ex: printf("Wrong parameters value: file %s on line %d\r\n", file, line) */
  /* USER CODE END 6 */
}
#endif /* USE_FULL_ASSERT */

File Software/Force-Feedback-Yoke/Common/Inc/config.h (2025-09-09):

/*
 * config.h
 *
 *  Created on: Jul 7, 2025
 *      Author: Jennyston
 */

#ifndef INC_CONFIG_H_
#define INC_CONFIG_H_

#include "hardware_config.h"

#define DRIVER_PITCH_BUS_VOLTAGE 24.0f
#define CURRENT_SENSE_PITCH_MAX_CURRENT 16.5f

#define PITCH_MOTOR_TORQUE_LIMIT 0.20f

#define MOTOR_PITCH_POLE_PAIRS 4
#define MOTOR_PITCH_KT 0.166666667f
#define PITCH_ELECTRICAL_ANGLE_OFFSET (-14739)

#define DRIVER_ROLL_BUS_VOLTAGE 24.0f
#define CURRENT_SENSE_ROLL_MAX_CURRENT 16.5f

#define ROLL_MOTOR_TORQUE_LIMIT 0.40f

#define MOTOR_ROLL_POLE_PAIRS 4
#define MOTOR_ROLL_KT 0.166666667f
//#define ROLL_ELECTRICAL_ANGLE_OFFSET (-15402)
#define ROLL_ELECTRICAL_ANGLE_OFFSET (-934)

#define PITCH_STEP_PER_MM ((ENCODER_PITCH_COUNTS_PER_REV*3)/(3.14159f*19.10f))
#define PITCH_MM_PER_REV ((3.14159f*19.10f)/3)
#define ROLL_STEP_PER_DEGREE ((ENCODER_ROLL_COUNTS_PER_REV*4)/(360.0f))
#define ROLL_DEGREE_PER_REV (360.0f/4)

#define PITCH_YOKE_FORCE_PER_MOTOR_TORQUE 314.13612565f
#define ROLL_YOKE_TORQUE_PER_MOTOR_TORQUE 4.0f


#define SERIAL_TX_BUFFER_SIZE 64
#define SERIAL_RX_BUFFER_SIZE 64

// *** PID ***
// Current/Torque Control PID
#define MOTOR_PITCH_ID_KP 10.0f
#define MOTOR_PITCH_ID_KI 0.6f
#define MOTOR_PITCH_ID_KD 0.0f
#define MOTOR_PITCH_ID_INTEGRAL_LIMIT 10.0f

#define MOTOR_PITCH_IQ_KP 16.0f
#define MOTOR_PITCH_IQ_KI 5.0f
#define MOTOR_PITCH_IQ_KD 0.0f
#define MOTOR_PITCH_IQ_INTEGRAL_LIMIT 10.0f

#define MOTOR_ROLL_ID_KP 10.0f
#define MOTOR_ROLL_ID_KI 0.6f
#define MOTOR_ROLL_ID_KD 0.0f
#define MOTOR_ROLL_ID_INTEGRAL_LIMIT 10.0f

#define MOTOR_ROLL_IQ_KP 16.0f
#define MOTOR_ROLL_IQ_KI 5.0f
#define MOTOR_ROLL_IQ_KD 0.0f
#define MOTOR_ROLL_IQ_INTEGRAL_LIMIT 10.0f

// Velocity Control PID
//#define MOTOR_PITCH_VELOCITY_KP 0.008
#define MOTOR_PITCH_VELOCITY_KP 0.012f
#define MOTOR_PITCH_VELOCITY_KI 0.05f
#define MOTOR_PITCH_VELOCITY_KD 0.000f
#define MOTOR_PITCH_VELOCITY_INTEGRAL_LIMIT 20.0f
#define MOTOR_PITCH_VELOCITY_EPSILON 0.0005f

//#define MOTOR_ROLL_VELOCITY_KP 0.008
#define MOTOR_ROLL_VELOCITY_KP 0.012f
#define MOTOR_ROLL_VELOCITY_KI 0.05f
#define MOTOR_ROLL_VELOCITY_KD 0.000f
#define MOTOR_ROLL_VELOCITY_INTEGRAL_LIMIT 20.0f
#define MOTOR_ROLL_VELOCITY_EPSILON 0.0005f

// *** Filter Configuration ***
// Current Sense Filter Configuration
#define CURRENT_SENSE_PITCH_LPF_ALPHA 0.98f
#define CURRENT_SENSE_ROLL_LPF_ALPHA 0.98f

// Velocity Filter Configuration
#define MOTOR_PITCH_VELOCITY_LPF_ALPHA 0.92f
#define MOTOR_ROLL_VELOCITY_LPF_ALPHA 0.92f

// Load Cell Filter Configuration
#define LOAD_CELL_LPF_ALPHA 0.94f

// *** Loop Frequency Division ***
#define MOTOR_PITCH_VELOCITY_LOOP_FREQ_DIV 20
#define MOTOR_ROLL_VELOCITY_LOOP_FREQ_DIV 20

// *** FFB Assist Configuration ***
#define FFB_ASSIST_GAIN 0.00100f
#define FFB_ASSIST_ACCEL_GAIN (-12000.0f)
#define FFB_ASSIST_VELOCITY_GAIN 5.0f
#define FFB_ASSIST_VELOCITY_SMALL_COMP 0.00001f

// *** FFB Home Configuration
#define FFB_PITCH_HOME_SPRING 0.01f
#define FFB_PITCH_HOME_DAMPER 0.0001f

#define FFB_ROLL_HOME_SPRING 0.001f
#define FFB_ROLL_HOME_DAMPER 0.00001f


#endif /* INC_CONFIG_H_ */

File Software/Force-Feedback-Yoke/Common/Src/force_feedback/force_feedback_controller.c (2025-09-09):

/*
 * force_feedback_controller.c
 *
 *  Created on: May 24, 2023
 *      Author: Jennyston
 */

#include "utilities/utilities.h"
#include "force_feedback/force_feedback_controller.h"
#include "delay.h"
#include <math.h>
#include <string.h>


static float ConvertFFBToMotorVelocity(FFBController_t *ffb,
		float ffbVelocity);

static float ConvertMotorToFFBVelocity(FFBController_t *ffb,
		float motorVelocity);

static float ConvertEncoderCountsToFFBUnits(FFBController_t *ffb,
		int counts);

static void FFB_SetMotorCurrent(FFBController_t *ffb, float current);
static void FFB_SetMotorTorque(FFBController_t *ffb, float torque);
static void FFB_SetMotorVelocity(FFBController_t *ffb, float velocity);
static float FFB_GetMotorVelocity(FFBController_t *ffb);
static float FFB_GetMotorTorque(FFBController_t *ffb);

void UpdateFFBSpeed(FFBController_t *ffb, float dt) {

	int currentEncoderCount = FFB_GetRawAxisCount(ffb);

	float currentSpeed = FFB_GetMotorVelocity(ffb);

	// Calculate acceleration
	ffb->acceleration = LowPassFilter_Update(&ffb->lpfAccel,
			(currentSpeed - ffb->speed)/dt);

	// Update previous variables
	ffb->prevEncoderCount = currentEncoderCount;
	ffb->speed = currentSpeed;
}

void FFB_Init(FFBController_t *ffb, Motor_t *motor, Encoder_t *encoder) {
	ffb->state = FFB_STOPPED;
	ffb->homingState = FFB_UNHOMED;

	ffb->motor = motor;
	ffb->encoder = encoder;
	ffb->loadCell = NULL;

	ffb->axisReverse = false;

	ffb->constantGain = 1.0f;
	ffb->periodicGain = 0.0f;
	ffb->springGain = 1.0f;
	ffb->damperGain = 1.0f;

	ffb->gain = 1.0f;
	ffb->motorKtConstant = 0.0265;
	ffb->minLock = -200000;
	ffb->maxLock = 200000;
	ffb->travelRange = 0;
	ffb->lockPower = 1.0f;
	ffb->lockKp = 0.000002f;
	ffb->lockKd = 0.002f;
	ffb->lockHysterisis = 8000;

	ffb->unitPerNm = 1;
	ffb->unitPerRev = 1;

	ffb->prevEncoderCountAvg = FFB_GetRawAxisCount(ffb);
	ffb->speed = 0;
	LowPassFilter_Init(&ffb->lpfSpeed, 0.10f);
	ffb->acceleration = 0;
	LowPassFilter_Init(&ffb->lpfAccel, 0.875f);

	ffb->speedDt = 0;

	// Initialize all forces to 0
	FFBForces_t forces = {
			.constantForce = 0,
			.springForce = 0,
			.damperForce = 0,
	};
	FFB_SetForces(ffb, forces);

//	FFB_SetConstant(ffb, 0);
////	FFBPeriodicInit(&ffb->param.periodic, 0, 0, 0);
//	FFB_SetSpring(ffb, 0);
//	FFB_SetDamper(ffb, 0);

	ffb->assistEnable = false;
	FFBAssist_Init(&ffb->ffbAssist);
}


void FFB_SetAxisReverse(FFBController_t *ffb, bool reverse) {
	ffb->axisReverse = reverse;
}

int FFB_GetRawAxisCount(FFBController_t *ffb) {
	return ffb->axisReverse ? -Encoder_GetCount(ffb->encoder) :
			Encoder_GetCount(ffb->encoder);
}

void FFB_SetAxisCount(FFBController_t *ffb, int count) {
	ffb->axisReverse ? Encoder_SetCount(ffb->encoder, -count) :
			Encoder_SetCount(ffb->encoder, count);
}

void FFB_SetLoadCell(FFBController_t *ffb, LoadCell_t *loadCell) {
	ffb->loadCell = loadCell;
}

void FFB_SetLockGains(FFBController_t *ffb, float lockKp, float lockKd) {
	ffb->lockKp = lockKp;
	ffb->lockKd = lockKd;
}

void FFB_SetAssistEnable(FFBController_t *ffb, bool enabled) {
	// Only enable assist if a load cell has been set
	ffb->assistEnable = enabled & (ffb->loadCell != NULL);
}

FFBAssist_t *FFB_GetFFBAssist(FFBController_t *ffb) {
	return &ffb->ffbAssist;
}

void FFB_SetConstant(FFBController_t *ffb, float force) {
	ffb->forces.constantForce = force;
}

//void FFBSetPeriodicParams(FFBController_t *ffb, FFBPeriodicForce_t periodic) {
//	ffb->param.periodic = periodic;
//}
//
void FFB_SetSpring(FFBController_t *ffb, float spring) {
	ffb->forces.springForce= spring;
}

void FFB_SetDamper(FFBController_t *ffb, float damperStrength) {
	ffb->forces.damperForce = damperStrength;
}

void FFB_SetForces(FFBController_t *ffb, FFBForces_t forces) {
	ffb->forces = forces;
}

void FFB_SetHomeCenterForces(FFBController_t *ffb, FFBForces_t homeCenterForces) {
	ffb->homeCenterForce = homeCenterForces;
}

float FFB_CalcForces(FFBController_t *ffb, float measuredPosition,
		float deltaTime) {

		float constantForce = FFB_CalcConstantForce(ffb->constantGain,
				ffb->forces.constantForce);

		// TODO: Implement periodic force type
		float periodicForce = 0.0f;
//		float periodicForce = FFBCalcPeriodicForce(ffb->periodicGain,
//				&ffb->param.periodic, deltaTime);

		float springForce = FFB_CalcSpringForce(ffb->springGain,
				ConvertEncoderCountsToFFBUnits(ffb, measuredPosition),
				ffb->forces.springForce);

		float damperForce = FFB_CalcDamperForce(ffb->damperGain,
				ffb->forces.damperForce, ffb->speed);


		// Assist force gain is independent to prevent runaway
		float force = ffb->gain *
				(constantForce + periodicForce + springForce + damperForce);

		// Update force output from main forces
		ffb->forceOut = force;

		if(ffb->assistEnable) {

			force += FFBAssist_Calc(&ffb->ffbAssist,
					-LoadCell_GetValue(ffb->loadCell),
					FFB_GetMotorTorque(ffb),
					ffb->speed, ffb->acceleration, deltaTime);
		}

		// Check if axis is outside lock range
		float lockDampening = 0.0f;
		if(measuredPosition > ffb->minLock + ffb->lockHysterisis) {
			ffb->minLockReached = false;
		}
		else if(measuredPosition < ffb->minLock) {
			ffb->minLockReached = true;
			lockDampening = ffb->lockKd * ffb->speed;
		}
		else {
			lockDampening = ffb->lockKd * ffb->speed;
			return fmaxf(force, 0) - lockDampening ;
		}

		if(measuredPosition < ffb->maxLock - ffb->lockHysterisis) {
			ffb->maxLockReached = false;
		}
		else if(measuredPosition > ffb->maxLock) {
			ffb->maxLockReached = true;
			lockDampening = ffb->lockKd * ffb->speed;
		}
		else {
			lockDampening = ffb->lockKd * ffb->speed;
			return fminf(force, 0) - lockDampening;
		}

		if(ffb->minLockReached) {
			return fmaxf(fmaxf(force, 0) + ffb->lockKp *
					powf(ffb->minLock - measuredPosition, 2.0f),
					0) - lockDampening;
		}
		else if (ffb->maxLockReached) {
			return fminf(fminf(force, 0) -
					ffb->lockKp * powf(ffb->maxLock - measuredPosition, 2.0f),
					0) - lockDampening;
		}
		else {
			return force - lockDampening;
		}
}

void FFB_Update(FFBController_t *ffb, float deltaTimeMs) {
	UpdateFFBSpeed(ffb, deltaTimeMs);
	if(ffb->loadCell != NULL) {
		LoadCell_Update(ffb->loadCell);
	}

	switch(ffb->state){
	case FFB_STOPPED:
		break;
	case FFB_RUNNING:
		float force =
				ConstrainFloat(FFB_CalcForces(ffb,
						FFB_GetRawAxisCount(ffb),
						deltaTimeMs), -60.0f,
						60.0f);
		FFB_SetMotorTorque(ffb, FFB_ConvertFFBToMotorTorque(ffb, force));
		break;
	case FFB_IDLE:
		break;
	default:
		// Should not reach here
		Motor_SetVoltage(ffb->motor, 0);
		break;
	}
}

void FFB_Stop(FFBController_t *ffb) {
	ffb->state = FFB_STOPPED;
	Motor_SetVoltage(ffb->motor, 0);
	Motor_SetEnable(ffb->motor, false);
}

void FFB_Start(FFBController_t *ffb) {
	ffb->state = FFB_RUNNING;
	Motor_SetEnable(ffb->motor, true);
}

FFBControllerState_e FFB_GetState(FFBController_t *ffb) {
	return ffb->state;
}

void FFB_SetControlRange(FFBController_t *ffb, int min, int max) {
	ffb->minLock = min;
	ffb->maxLock = max;
}
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

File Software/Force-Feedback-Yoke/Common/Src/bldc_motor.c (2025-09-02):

/*
 * bldc.c
 *
 *  Created on: Jul 9, 2025
 *      Author: Jennyston
 */

#include "bldc_motor.h"
#include <stddef.h>
#include <math.h>
#include "bldc_foc_math.h"
#include "utilities/utilities.h"
#include "delay.h"

static int CalcElectricalAngleRawCount(BLDCMotor_t *motor);
static int CalcElectricalAngleCount(BLDCMotor_t *motor);
static float CalcElectricalAngle(BLDCMotor_t *motor);

void BLDCMotor_Init(BLDCMotor_t *motor, BLDCDriver_t *driver,
		Encoder_t *encoder, int polePairs) {
	motor->driver = driver;
	motor->encoder = encoder;
	motor->electricalAngleOffsetCount = 0;
	motor->electricalAngleCount = 0;
	motor->electricalAngle = 0.0f;

	motor->currentA = NULL;
	motor->currentB = NULL;
	motor->currentC = NULL;

	motor->kt = 0.0f;
	motor->qCurrentLimit = 0.5f;
	motor->polePairs = polePairs;
	motor->mode = BLDC_MOTOR_MODE_VOLTAGE;

	motor->eStop = false;
	motor->voltage = 0.0f;

	FOC_Init(&motor->foc, BLDCDriver_GetBusVoltage(driver));
}

void BLDCMotor_SetCurrentSensors(BLDCMotor_t *motor, CurrentSensor_t *currentA,
		CurrentSensor_t *currentB, CurrentSensor_t *currentC) {
	motor->currentA = currentA;
	motor->currentB = currentB;
	motor->currentC = currentC;
}

void BLDCMotor_SetEnable(BLDCMotor_t *motor, bool enabled) {
	BLDCDriver_SetEnable(motor->driver, enabled & !motor->eStop);
}

void BLDCMotor_SetEStop(BLDCMotor_t *motor, bool eStop) {
	motor->eStop = eStop;

	BLDCDriver_SetEnable(motor->driver, eStop);
	BLDCMotor_SetVoltage(motor, 0.0f);

}

void BLDCMotor_SetTorqueConstant(BLDCMotor_t *motor, float kt) {
	motor->kt = kt;
}

void BLDCMotor_SetElectricalAngleOffsetCount(BLDCMotor_t *motor, int offset) {
	motor->electricalAngleOffsetCount = offset;
}

int BLDCMotor_GetElectricalAngleOffsetCount(BLDCMotor_t *motor) {
	return motor->electricalAngleOffsetCount;
}

float BLDCMotor_GetBusVoltage(BLDCMotor_t *motor) {
	return BLDCDriver_GetBusVoltage(motor->driver);
}

void BLDCMotor_SetVoltage(BLDCMotor_t *motor, float voltage) {
	motor->mode = BLDC_MOTOR_MODE_VOLTAGE;
	motor->voltage = voltage;
}

float BLDCMotor_GetVoltage(BLDCMotor_t *motor) {
	return motor->voltage;
}

void BLDCMotor_SetDCurrent(BLDCMotor_t *motor, float current) {
	motor->mode = BLDC_MOTOR_MODE_CURRENT;
	FOC_SetIDSetPoint(&motor->foc, current);
}

float BLDCMotor_GetDCurrent(BLDCMotor_t *motor) {
	return FOC_GetIDSetPoint(&motor->foc);
}

void BLDCMotor_SetQCurrentLimit(BLDCMotor_t *motor, float currentLimit) {
	motor->qCurrentLimit = currentLimit;
}

float BLDCMotor_GetQCurrentLimit(BLDCMotor_t *motor) {
	return motor->qCurrentLimit;
}

void BLDCMotor_SetQCurrent(BLDCMotor_t *motor, float current) {
	motor->mode = BLDC_MOTOR_MODE_CURRENT;

	FOC_SetIQSetPoint(&motor->foc,
			ConstrainFloat(current, -motor->qCurrentLimit,
					motor->qCurrentLimit));
}

float BLDCMotor_GetQCurrent(BLDCMotor_t *motor) {
	return FOC_GetIQSetPoint(&motor->foc);
}

int BLDCMotor_GetNumCurrentSensors(BLDCMotor_t *motor) {
	return motor->currentA == NULL ? 0 : 2;
}

void BLDCMotor_SetTorque(BLDCMotor_t *motor, float torque) {
	if(motor->kt > 0.0f) {
		BLDCMotor_SetQCurrent(motor, torque/motor->kt);
	}
	else {
		// Torque constant has not been set or is invalid
		BLDCMotor_SetQCurrent(motor, 0.0f);
	}
}

float BLDCMotor_GetTorque(BLDCMotor_t *motor) {
	return FOC_GetIQSetPoint(&motor->foc) * motor->kt;
}

float BLDCMotor_GetTorqueReading(BLDCMotor_t *motor) {
	return BLDCMotor_GetQCurrentReading(motor) * motor->kt;
}

void BLDCMotor_SetTorqueLimit(BLDCMotor_t *motor, float torqueLimit) {
	motor->qCurrentLimit = torqueLimit/motor->kt;
}

float BLDCMotor_GetTorqueLimit(BLDCMotor_t *motor) {
	return motor->qCurrentLimit/motor->kt;
}

float BLDCMotor_GetDCurrentReading(BLDCMotor_t *motor){
	return FOC_GetDQCurrent(&motor->foc).d;
}

float BLDCMotor_GetQCurrentReading(BLDCMotor_t *motor) {
	return FOC_GetDQCurrent(&motor->foc).q;
}

float BLDCMotor_GetTotalCurrentReading(BLDCMotor_t *motor) {
	float d_2 = BLDCMotor_GetDCurrentReading(motor) *
			BLDCMotor_GetDCurrentReading(motor);
	float q_2 = BLDCMotor_GetQCurrentReading(motor) *
			BLDCMotor_GetQCurrentReading(motor);
	return sqrtf(d_2 + q_2);
}

FOC_t *BLDCMotor_GetFOC(BLDCMotor_t *motor) {
	return &motor->foc;
}

void BLDCMotor_RunCurrentSensorCalibration(BLDCMotor_t *motor,
		unsigned int numSamples) {
	BLDCMotor_SetVoltage(motor, 0.0f);
	BLDCMotor_SetEnable(motor, true);

	delayMs(500);

	CurrentSensor_Calibrate(motor->currentA, numSamples);
	CurrentSensor_Calibrate(motor->currentB, numSamples);
	CurrentSensor_Calibrate(motor->currentC, numSamples);
}

void BLDCMotor_RunEncoderCalibration(BLDCMotor_t *motor,
		float phaseHoldCurrent) {
	motor->mode = BLDC_MOTOR_MODE_ENCODER_CAL;

//	PhaseVoltages_t phaseVoltages = {
//			.a = phaseHoldVoltage * cosf(0),
//			.b = phaseHoldVoltage * cosf(-2.0f*((float)M_PI)/3.0f),
//			.c = phaseHoldVoltage * cosf(2.0f*((float)M_PI)/3.0f)
//	};

	BLDCDriver_SetEnable(motor->driver, true);

	FOC_SetIQSetPoint(&motor->foc, 0.0f);
	FOC_SetIDSetPoint(&motor->foc, phaseHoldCurrent);

	delayMs(2500);
	motor->electricalAngleOffsetCount = -CalcElectricalAngleRawCount(motor);

	FOC_SetIDSetPoint(&motor->foc, 0.0f);
	BLDCDriver_SetVoltages(motor->driver, 0, 0, 0);
}

void BLDCMotor_Update(BLDCMotor_t *motor, float deltaTimeMs) {

	// Check if current sensors have been assigned
	if(motor->currentA != NULL) {
		// Update sensors
		CurrentSensor_Update(motor->currentA, deltaTimeMs);
		CurrentSensor_Update(motor->currentB, deltaTimeMs);
		CurrentSensor_Update(motor->currentC, deltaTimeMs);

		// Get phase currents
		motor->phaseCurrents.a = CurrentSensor_GetValue(motor->currentA);
		motor->phaseCurrents.b = CurrentSensor_GetValue(motor->currentB);
		motor->phaseCurrents.c = CurrentSensor_GetValue(motor->currentC);
	}

	motor->electricalAngleCount = CalcElectricalAngleCount(motor);
	motor->electricalAngle = CalcElectricalAngle(motor);

	if(motor->mode == BLDC_MOTOR_MODE_CURRENT) {

		PhaseVoltages_t phaseVoltages =
				FOC_Calc(&motor->foc, motor->phaseCurrents,
						motor->electricalAngle,
						deltaTimeMs);
		BLDCDriver_SetVoltages(motor->driver, phaseVoltages.a, phaseVoltages.b,
				phaseVoltages.c);
	}
	else if(motor->mode == BLDC_MOTOR_MODE_VOLTAGE) {

		// Calculate phase voltages
		PhaseVoltages_t phaseVoltages = FOCMath_CalcPhaseVoltages(0.0f,
				motor->voltage/2.0f,
				motor->electricalAngle);

		// Assign phase voltages
		BLDCDriver_SetVoltages(motor->driver, phaseVoltages.a,
					phaseVoltages.b, phaseVoltages.c);
	}
	else if(motor->mode == BLDC_MOTOR_MODE_ENCODER_CAL) {
		PhaseVoltages_t phaseVoltages =
				FOC_Calc(&motor->foc, motor->phaseCurrents,
						0.0f,
						deltaTimeMs);
		BLDCDriver_SetVoltages(motor->driver, phaseVoltages.a, phaseVoltages.b,
				phaseVoltages.c);
	}
	else {
		FOC_ResetPID(&motor->foc);
		// Do Nothing
	}
}
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

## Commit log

2023-05-24 Unit testing added. Force feedback spring force tested.
2023-05-25 Current sensing added (not yet implemented). Damper and spring force added.
2023-06-20 Major changes made. Code currently configured to run alongside MSFSForceFeedbackController.
2023-06-20 AS5048A breakout board added.
    [AS5048A Breakout.kicad_pcb, AS5048A Breakout.kicad_sch, PCB Outline.dxf]
2023-06-23 Current sensor schematic complete.
    [Current Sensor.kicad_pcb, Current Sensor.kicad_sch]
2023-09-29 USB device backup updated.
2023-09-29 Fixed bug with FFBComputeSpringForce parameters switched. Reverted USB report descriptor.
    [main.c]
2023-10-02 Endstop feature added.
2023-10-13 Added time divider for counting time in ms in timer 6 ISR.
2023-10-13 Removed time divider logic from timer 6 ISR. Replaced time measurement code with HAL_GetTick()
    [Force Feedback Yoke.ioc, main.c]
2024-07-12 Added encoder with unit tests.
2024-07-13 Added AS5600 encoder.
2024-07-16 Modified pin labels, added accept button.
2024-07-16 Added code for handling buttons.
2024-07-16 Migrated code from main to app and bsp (Board Support Package).
2024-07-19 Created FFBPeriodicUpdateTime function to keep track of time for periodic forces.
2024-07-25 Added call to ApplicationUpdate function from timer interrrupt callback.
2024-08-01 Migrated device firmware to STM32F411CE.
2024-08-10 Added direction power scale.
2024-08-10 Changed motor power max due to change in PWM resolution.
2024-08-10 Added application update functions to timer ISR.
2024-08-10 Fixed PWM not starting.
    [bsp.c]
2024-10-23 Added Google Test framework.
2024-10-26 Modified device configuration.
2024-10-26 Changed to obtain sensor count through interface instead.
2024-10-26 Added motor driver enable pins.
2024-10-26 Backup of USB device library files (STM32CubeIDE code regeneration replaces modified library files).
2025-08-25 Updated schematic and PCB files for current hardware configuration.
    [AS5048A Breakout.kicad_pcb, AS5048A Breakout.kicad_sch, Current Sensor.kicad_pcb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]
2025-08-25 Moved code for other hardware platforms to unused.
    [anticog_ptch_data.csv]
2025-08-25 Migrated to STM32H7 platform, added many features.
    - Switched from brushed to brushless motors for both pitch and roll axes. Controller now uses torque control with current sensing
    - Changed encoder hardware to MT6835 for position sensing. Now using AB quadrature output for lower latency.
    - Modified load cell based force feedback assist calculations.
    - Changed USB communication protocol to handle 3 different force types (currently for one axis) using HID interrupt transfers. Switched over to control transfers for configuration.
    [anticog_ptch_data.csv]
2025-09-01 Modified velocity PID, added FFB Home Configuration.
2025-09-01 Modified home velocity, changed home center logic.
2025-09-02 Switched from current to torque units.
2025-09-02 Roll torque indicators now update.
2025-09-07 Added save button enable logic.
2025-09-07 Switched to Range class.
2025-09-07 Added calibration airspeed parameter.
2025-09-09 Fixed bug with NaN forces on initialization.
    [force_feedback_controller.c]
2025-09-09 Switched PID tuner DAQ to roll motor.
2025-09-09 Modified roll torque limit, removed current limit defines.
2025-09-09 Fixed bug on device disconnect and connect.

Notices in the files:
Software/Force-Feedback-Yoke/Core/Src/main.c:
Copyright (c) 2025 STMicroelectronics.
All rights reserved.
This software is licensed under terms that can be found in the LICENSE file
